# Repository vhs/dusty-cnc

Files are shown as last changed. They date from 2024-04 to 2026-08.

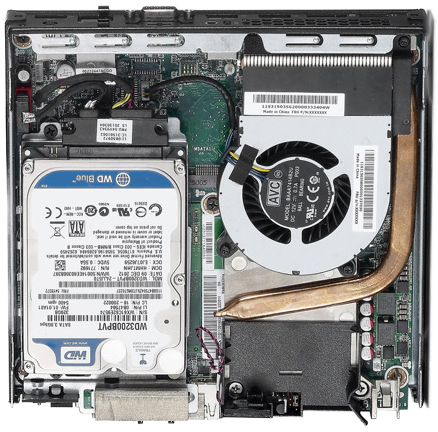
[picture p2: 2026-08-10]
documentation/wiring-diagram/components/Lenovo m73.png

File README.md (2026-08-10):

This repo contains files related to Dusty, the VHS wood CNC router.

- The repo is in a state of flux during the CNC rebuilding project
  - Files may move, disappear, or be created in large quantities
  - The machine name and repo name will change on release
  - It is always worth verifying with the project manager if you have up-to-date information
- Primary software used:
  - CAD software capable of reading/writing STEP files (such as FreeCAD, Rhino, Solidworks or Fusion360)
  - Draw.io (desktop or online) FOSS diagram software
  - Apple Numbers (an .xlsx export of the wiring chart exists for those who cannot access the main document, but should not be updated directly… this needs to be rectified)
- Notable files in the repo:
  - [Wiring Chart & BOM](https://github.com/vhs/dusty-cnc/blob/main/documentation/wiring-diagram/Dustie%20Wiring%20Chart.numbers) ([or read-only excel format](https://github.com/vhs/dusty-cnc/blob/main/documentation/wiring-diagram/Dustie%20Wiring%20Chart.export.xlsx))
  - [Wiring Diagram](https://github.com/vhs/dusty-cnc/blob/main/documentation/wiring-diagram/Wiring%20Diagram.drawio)
  - [CAD Assembly](https://github.com/vhs/dusty-cnc/blob/main/cad/Dustie%20Assembly.step) (not up to date)
- Notes:
  - Any questions please reach out to Martin ([@imagesurgery](https://github.com/imagesurgery))

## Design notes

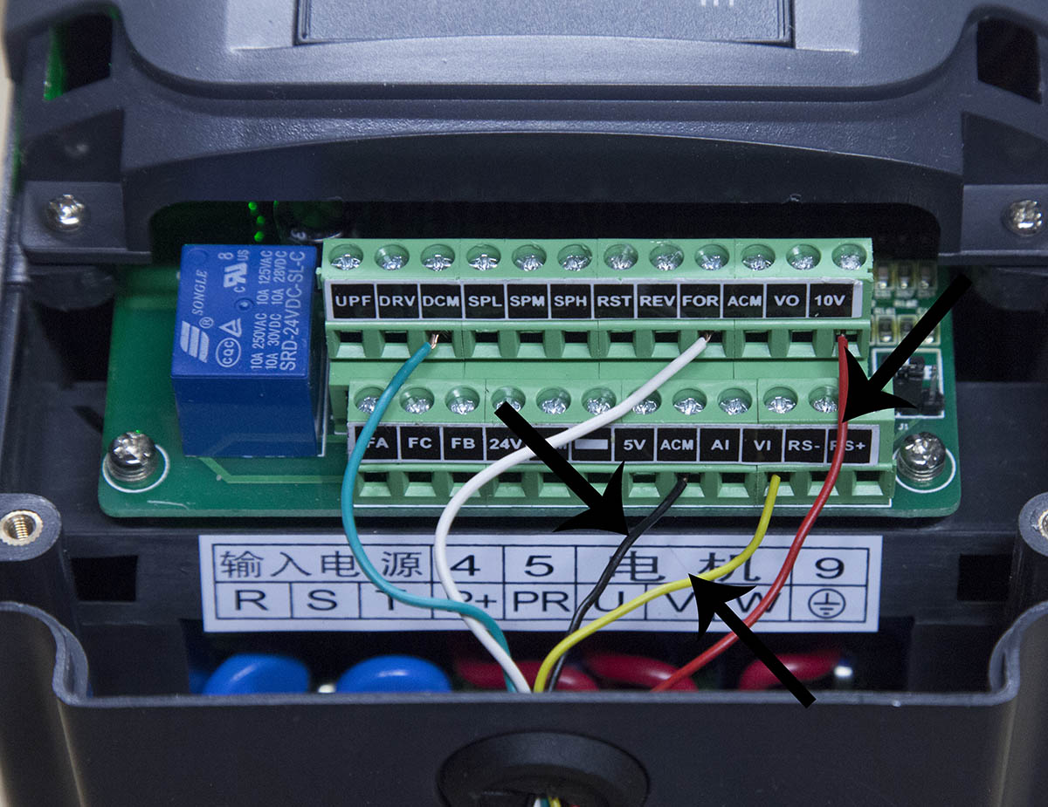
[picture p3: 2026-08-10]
documentation/manuals-datasheets/spindle/HY02D223B-pinout.jpeg

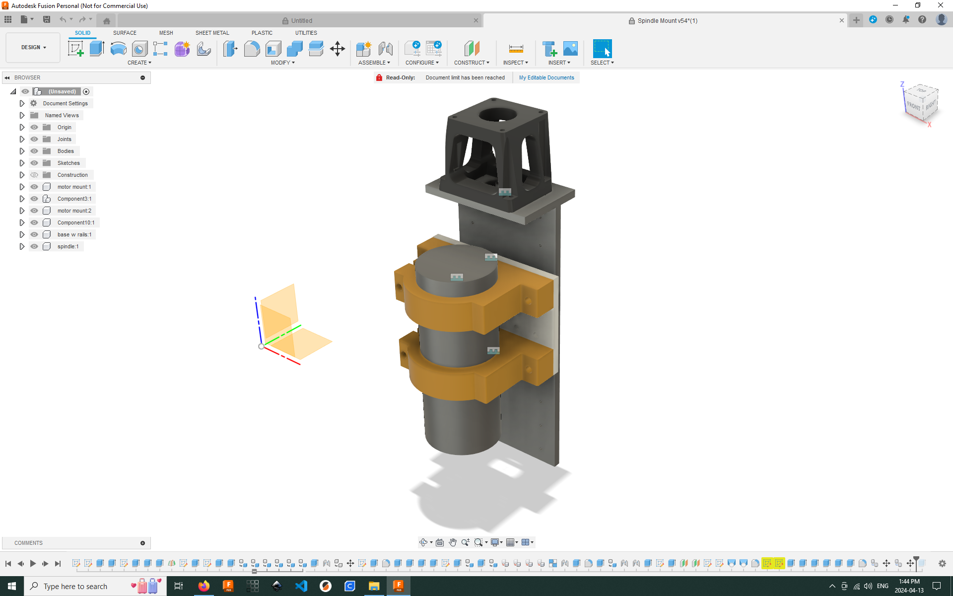
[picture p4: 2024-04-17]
Spindle Mount/spindle_mount_v54_preview.png

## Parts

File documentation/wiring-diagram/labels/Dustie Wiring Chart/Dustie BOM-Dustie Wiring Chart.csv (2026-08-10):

Tag | Type | Part / Model | Description | Mfr | Rating | Location | Mounting | Terminals | Used In | Qty | Spare | Notes
CPU1 | CPU |  | Tiny Form Factor Computer | Lenovo |  | CPU Cabinet | DIN Rail w. Printed Mount
F1 | EMI Filter |  |  |  |  | Main Cabinet | DIN Rail w. Printed Mount | 1-4
FAN1 | Fan |  |  |  | 24 VDC | Filter Box
FAN2 | Fan |  |  |  | 24 VDC | Filter Box
FAN3 | Fan |  |  |  |  | Filter Box
FAN4 | Fan |  |  |  |  | Filter Box
HS1 | Inductive Sensor |  | Y1 Home Switch |  |  | Static Platform | 8040 w. Printed Mount
HS2 | Inductive Sensor |  | Y2 Home Switch |  |  | Static Platform | 8040 w. Printed Mount
HS3 | Inductive Sensor |  | X Home Switch |  |  | Y Platform | 8040 w. Printed Mount
HS4 | Inductive Sensor |  | Z Home Switch |  |  | X Platform | Printed Mount
IM1 | Integrated Stepper | JSS57P2N | Y1 Integrated Stepper | Generic |  | Y Platform |  | Dir,Pul,Ena,Pend,Alm:[+/-] 5V,Tx,Gnd_SIG,Rx,NC; GND_PWR,+VDC
IM2 | Integrated Stepper | JSS57P2N | Y2 Integrated Stepper | Generic |  | Y Platform
IM3 | Integrated Stepper | JSS57P2N | X Integrated Stepper | Generic |  | X Platform
J1 | Connector | DB25-F to TB | Stepper and Sensor Signals |  |  | Main Cabinet Breakout | Panel Mount | 1-25,GND
J10 | Connector | PTB-2 | Sensor Power |  |  | Static Platform | Panel Mount | 1-2
J11 | Connector | PTB-8 | Integrated Stepper Power, Z Stepper Motor |  |  | Static Platform | Panel Mount | 1-8
J12 | Connector | PTB-8 | Estop Loop |  |  | Static Platform | Panel Mount | 1-8
J13 | Connector | PTB-4 | Estop Loop |  |  | Static Platform | Panel Mount | 1-4
J14 | Connector | DB25-F to TB |  |  |  | Static Platform | Panel Mount | 1-25,GND
J15 | Connector | PTB-4 | Sensor Power, Y1, Y2 Integrated Stepper Power |  |  | Static Platform | Panel Mount | 1-4
J16 | Connector | PTB-8 | X Integrated Stepper Power, Z Stepper Motor |  |  | Static Platform | Panel Mount | 1-8
J17 | Connector | PTB-4 | Estop Loop |  |  | MPG | Panel Mount | 1-4
J19 | Connector | DB25-F to TB |  |  |  | Y Platform | Panel Mount | 1-25,GND
J2 | Connector | PTB-2 | Sensor Power |  |  | Main Cabinet Breakout | Panel Mount | 1-2
J20 | Connector | PTB-4 | Sensor Power, Y1, Y2 Integrated Stepper Power |  |  | Y Platform | Panel Mount | 1-4
J24 | Connector | DB9-F to TB |  |  |  | Y Platform | Panel Mount | 1-9
J25 | Connector | PTB-2 | Sensor Power |  |  | Y Platform | Panel Mount | 1-2
J28 | Connector | DB9-F to TB |  |  |  | X Platform | Panel Mount | 1-9
J29 | Connector | PTB-2 | Sensor Power |  |  | X Platform | Panel Mount | 1-2
J3 | Connector | PTB-8 | Integrated Stepper Power, Z Stepper Motor |  |  | Main Cabinet Breakout | Panel Mount | 1-8
J30 | Connector | PTB-8 | X Integrated Stepper Power, Z Stepper Motor |  |  | X Platform | Panel Mount | 1-8
J35 | Connector |  | IEC C13 Socket |  |  | Main Cabinet Breakout | Panel Mount
J36 | Connector |  | IEC C7 Plug |  |  | Static Platform
J37 | Connector |  | HDMI Socket |  |  | Main Cabinet Breakout | Panel Mount | HDMI
J38 | Connector |  | USB Socket |  |  | Main Cabinet Breakout | Panel Mount | USB
J39 | Connector |  | USB Socket |  |  | CPU Cabinet | Panel Mount | USB
J4 | Connector | PTB-2 | Coolant Pump Relay |  |  | Main Cabinet Breakout | Panel Mount | 1-2
J5 | Connector | PTB-2 | Spindle Control |  |  | Main Cabinet Breakout | Panel Mount | 1-2
J6 | Connector | PTB-4 | X Integrated Stepper Power |  |  | Main Cabinet Breakout | Panel Mount | 1-4
J7 | Connector | PTB-8 | Estop Loop |  |  | Main Cabinet Breakout | Panel Mount | 1-8
J9 | Connector | DB25-F to TB |  |  |  | Static Platform | Panel Mount | 1-25,GND
K1 | Contactor |  |  |  |  | Main Cabinet | DIN Rail | L1-3,T1-3,13-14,21-22,A1,A2
K2 | Relay |  | Coolant Pump Relay |  |  |  |  |  |  |  |  | Need relay suitable for AC120V
LS1 | Inductive Sensor |  | Y- Limit Switch |  |  | Static Platform | 8040 w. Printed Mount
LS2 | Inductive Sensor |  | Y+ Limit Switch |  |  | Static Platform | 8040 w. Printed Mount
LS3 | Inductive Sensor |  | X- Limit Switch |  |  | Y Platform | 8040 w. Printed Mount
LS4 | Inductive Sensor |  | X+ Limit Switch |  |  | Y Platform | 8040 w. Printed Mount
LS5 | Inductive Sensor |  | Z- Limit Switch |  |  | X Platform | Printed Mount
LS6 | Inductive Sensor |  | Z+ Limit Switch |  |  | X Platform | Printed Mount
M1 | Spindle |  |  |  |  | Z Platform |  | 1(U),2(V),3(W),GND
MESA | FPGA Controller Card | 7i76EU |  | Mesa |  | Main Cabinet | DIN Rail w. Printed Mount | TB1,4:01-08;TB2-3,5-6:01-24
MON1 | Monitor |  | Touch Screen Monitor | Premio |  | Static Platform
P0 | Connector | HBL5666C | Nema 6-15P Plug | Hubbell |  | Power Entry |  | L1,L2,PE
P1 | Connector | DB25-M to TB |  |  |  | Main Cabinet Breakout | Panel Mount | 1-25,GND
P10 | Connector | PTB-2 | Sensor Power |  |  | Static Platform | Panel Mount | 1-2
P11 | Connector | PTB-8 | Integrated Stepper Power, Z Stepper Motor |  |  | Static Platform | Panel Mount | 1-8
P12 | Connector | PTB-8 | Estop Loop |  |  | Static Platform | Panel Mount | 1-8
P13 | Connector | PTB-4 | Estop Loop |  |  | Static Platform | Panel Mount | 1-4
P14 | Connector | DB25-M to TB |  |  |  | Static Platform | Panel Mount | 1-25,GND
P15 | Connector | PTB-4 | Sensor Power, Y1, Y2 Integrated Stepper Power |  |  | Static Platform | Panel Mount | 1-4
P16 | Connector | PTB-8 | X Integrated Stepper Power, Z Stepper Motor |  |  | Static Platform | Panel Mount | 1-8
P17 | Connector | PTB-4 | Estop Loop |  |  | MPG | Panel Mount | 1-4
P19 | Connector | DB25-M to TB |  |  |  | Y Platform | Panel Mount | 1-25,GND
P2 | Connector | PTB-2 | Sensor Power |  |  | Main Cabinet Breakout | Panel Mount | 1-2
P20 | Connector | PTB-4 | Sensor Power |  |  | Y Platform | Panel Mount | 1-4
P24 | Connector | DB9-M to TB |  |  |  | Y Platform | Panel Mount | 1-9
P25 | Connector | PTB-2 | Sensor Power |  |  | Y Platform | Panel Mount | 1-2
P28 | Connector | DB9-M to TB |  |  |  | X Platform | Panel Mount | 1-9
P29 | Connector | PTB-2 | Sensor Power |  |  | X Platform | Panel Mount | 1-2
P3 | Connector | PTB-8 | Y1, Y2 Integrated Stepper Power |  |  | Main Cabinet Breakout | Panel Mount | 1-8
P30 | Connector | PTB-8 | X Integrated Stepper Power |  |  | X Platform | Panel Mount | 1-8
P35 | Connector |  | IEC C14 Plug |  |  | Main Cabinet Breakout
P4 | Connector | PTB-2 | Coolant Pump Relay |  |  | Main Cabinet Breakout | Panel Mount | 1-2
P40 | Connector |  | IEC C5 Plug |  |  | CPU Cabinet |  | L,N,PE
P5 | Connector | PTB-2 | Spindle Control |  |  | Main Cabinet Breakout | Panel Mount | 1-2
P6 | Connector | PTB-4 | Spindle Power |  |  | Main Cabinet Breakout | Panel Mount | 1-4
P7 | Connector | PTB-8 | Estop Loop |  |  | Main Cabinet Breakout | Panel Mount | 1-8
P9 | Connector | DB25-M to TB |  |  |  | Static Platform | Panel Mount | 1-25,GND
PB1 | Momentary Button |  | Machine Start |  |  | Main Cabinet Door | Panel Mount | 13-14
PB2 | Momentary Button |  | Machine Stop |  |  | Main Cabinet Door | Panel Mount | 13-14
PL1 | Indicator Lamp |  | Main Estop Lamp |  |  | Main Cabinet Door | Panel Mount | X1-2
PL2 | Indicator Lamp |  | Machine Estop Lamp |  |  | Static Platform | Panel Mount | X1-2
PL3 | Indicator Lamp |  | MPG Estop Lamp |  |  | MPG | Panel Mount | X1-2
PL4 | Indicator Lamp |  | Machine Power Lamp |  |  | Main Cabinet Door | Panel Mount | X1-2
PS1 | PSU | HDR-15-24 | 24V 0.63A PSU | Mean Well | 24 VDC | Main Cabinet | DIN Rail
PS2 | PSU |  |  | Lenovo |  | CPU Cabinet | DIN Rail w. Printed Mount | L,N,PE
PS3 | PSU |  |  | Premio |  | Monitor Mount
PS4 | PSU |  |  | Mean Well | 24 VDC | Main Cabinet |  | L,N,GND,V+1,V+2,V-1,V-2
PS5 | PSU | S-350-48 | 48V 7.3A PSU | Generic | 48 VDC | Main Cabinet |  | L,N,GND,V+1,V+2,V+3,V-1,V-2,V-3
PS6 | PSU | S-350-48 | 48V 7.3A PSU | Generic | 48 VDC | Main Cabinet |  | L,N,GND,V+1,V+2,V+3,V-1,V-2,V-3
Q1 | MCB |  |  |  |  | Main Cabinet | DIN Rail | L1,L2,T1,T2
RF1 | Connector | ADP-SMAF-SMAF-F-G | WiFi Breakout |  |  | CPU Cabinet | Panel Mount | 1-2
RF2 | Antenna | SMA Antenna | WiFi Breakout |  |  | CPU Cabinet | SMA Screw Terminal | 1
S1 | Latching Estop |  | Main Estop |  |  | Main Cabinet Door | Panel Mount | 13-14,21-22
S2 | Latching Estop |  | Machine Estop |  |  | Static Platform | Box | 13-14,21-22
S3 | Latching Estop |  | MPG Estop |  |  | MPG | Panel Mount | 13-14,21-22
SD1 | Stepper Driver | HY-DIV268N-5A | Stepper Driver Z |  |  | Main Cabinet | DIN Rail w. Printed Mount | Dir,Pul,Ena,A,B,DC:[+/-]
SM1 | Stepper Motor | 57J1876-447-01 | Z Stepper Motor | Generic |  | X Platform
TB1 | Terminal Block | UK5N | 2-row DIN terminal | Phoenix Contact |  | Main Cabinet | DIN Rail | 1-6
TB10 | Terminal Block | UK5N | 2-row DIN terminal | Phoenix Contact |  | Main Cabinet | DIN Rail | 1-2
TB11 | Terminal Block | UK5N | 2-row DIN terminal | Phoenix Contact |  | Main Cabinet | DIN Rail | 1-26
TB2 | Terminal Block | UK5N | 2-row DIN terminal | Phoenix Contact |  | Main Cabinet | DIN Rail | 1-20
TB3 | Terminal Block | UK5N | 2-row DIN terminal | Phoenix Contact |  | Main Cabinet | DIN Rail | 1-20
TB4 | Terminal Block | UK5N | 2-row DIN terminal | Phoenix Contact |  | Main Cabinet | DIN Rail | 1-20
TB5 | Terminal Block | UK5N | 2-row DIN terminal | Phoenix Contact |  | Main Cabinet | DIN Rail | 1-18
TB51 | Terminal Block | PTFIX | 12P Push-in Distribution Block | Phoenix Contact |  | Static Platform |  | 1-12
TB52 | Terminal Block | PTFIX | 12P Push-in Distribution Block | Phoenix Contact |  | Static Platform |  | 1-12
TB53 | Terminal Block | PTFIX | 6P Push-in Distribution Block | Phoenix Contact |  | Y Platform |  | 1-6
TB54 | Terminal Block | PTFIX | 6P Push-in Distribution Block | Phoenix Contact |  | Y Platform |  | 1-6
TB55 | Terminal Block | PTFIX | 6P Push-in Distribution Block | Phoenix Contact |  | Y Platform |  | 1-6
TB56 | Terminal Block | PTFIX | 6P Push-in Distribution Block | Phoenix Contact |  | Y Platform |  | 1-6
TB57 | Terminal Block | PTFIX | 6P Push-in Distribution Block | Phoenix Contact |  | X Platform |  | 1-6
TB58 | Terminal Block | PTFIX | 6P Push-in Distribution Block | Phoenix Contact |  | X Platform |  | 1-6
TB6 | Terminal Block | UK5N | 2-row DIN terminal | Phoenix Contact |  | Main Cabinet | DIN Rail | 1-4
TB7 | Terminal Block | UK5N | 2-row DIN terminal | Phoenix Contact |  | Main Cabinet | DIN Rail | 1-6
TB8 | Terminal Block | UK5N | 2-row DIN terminal | Phoenix Contact |  | Main Cabinet | DIN Rail | 1-2
TB9 | Terminal Block | UK5N | 2-row DIN terminal | Phoenix Contact |  | Main Cabinet | DIN Rail | 1-2
TP1 | Passive Probe |  | Tool Touch Plate |  |  | Static Platform
TI1 | Temperature Indicator |  | Cabinet Temperature Sensor Module |  |  | Main Cabinet
VFD1 | VFD | HY02D223B |  | Huanyang | 220 VAC | VFD Cabinet | Metal Plate on VFD Cabinet | R,S,T,P+,PR,U,V,W,GND UPF,DRV,DCM,SPL,SPM,SPH,RST,REV,FOR,ACM,V0,10V FA,FC,FB,24V,COM,—,5V,ACM,AI,VI,RS-,RS+

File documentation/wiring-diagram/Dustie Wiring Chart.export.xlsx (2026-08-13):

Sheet: Export Summary
This document was exported from Numbers. Each table was converted to an Excel worksheet. All other objects on each Numbers sheet were placed on separate worksheets. Please be aware that formula calculations may differ in Excel.
Numbers Sheet Name | Numbers Table Name | Excel Worksheet Name
Dustie BOM
 | Dustie Wiring Chart | Dustie BOM - Dustie Wiring Char
Dustie Wires
 | Dustie Wiring Chart | Dustie Wires - Dustie Wiring Ch
Dustie Wire Labels
 | Dustie Wire Labels | Dustie Wire Labels - Dustie Wir

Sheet: Dustie BOM - Dustie Wiring Char
Dustie Wiring Chart
Tag | Type | Part / Model | Description | Location | Mounting | Terminals | Used In | Qty | Spare | Notes
CPU1 | CPU |  | Tiny Form Factor Computer | CPU Cabinet | DIN Rail w. Printed Mount
F1 | EMI Filter |  |  | Main Cabinet | DIN Rail w. Printed Mount | 1-4
FAN1 | Fan |  |  | Filter Box
FAN2 | Fan |  |  | Filter Box
FAN3 | Fan |  |  | Filter Box
FAN4 | Fan |  |  | Filter Box
HS1 | Inductive Sensor |  | Y1 Home Switch | Static Platform | 8040 w. Printed Mount
HS2 | Inductive Sensor |  | Y2 Home Switch | Static Platform | 8040 w. Printed Mount
HS3 | Inductive Sensor |  | X Home Switch | Y Platform | 8040 w. Printed Mount
HS4 | Inductive Sensor |  | Z Home Switch | X Platform | Printed Mount
IM1 | Integrated Stepper | JSS57P2N | Y1 Integrated Stepper | Y Platform |  | DIR,PUL,ENA,PEND,ALM:[+/-] 5V,TX,GND_SIG,RX,NC; GND_PWR,+VDC
IM2 | Integrated Stepper | JSS57P2N | Y2 Integrated Stepper | Y Platform
IM3 | Integrated Stepper | JSS57P2N | X Integrated Stepper | X Platform
J1 | Connector | DB25-F to TB | Stepper and Sensor Signals | Main Cabinet Breakout | Panel Mount | 1-25,GND
J10 | Connector | PTB-2 | Sensor Power | Static Platform | Panel Mount | 1-2
J11 | Connector | PTB-8 | Z, Dust Boot Stepper Motor | Static Platform | Panel Mount | 1-8
J12 | Connector | PTB-8 | Estop Loop | Static Platform | Panel Mount | 1-8
J13 | Connector | PTB-4 | Estop Loop | Static Platform | Panel Mount | 1-4
J14 | Connector | DB25-F to TB |  | Static Platform | Panel Mount | 1-25,GND
J15 | Connector | PTB-4 | Sensor Power, Y1, Y2 Integrated Stepper Power | Static Platform | Panel Mount | 1-4
J16 | Connector | PTB-8 | X Integrated Stepper Power, Z Stepper Motor | Static Platform | Panel Mount | 1-8
J17 | Connector | PTB-4 | Estop Loop | MPG | Panel Mount | 1-4
J18 | Connector | PTB-4 | Integrated Stepper Power | Static Platform | Panel Mount | 1-4
J19 | Connector | DB25-F to TB |  | Y Platform | Panel Mount | 1-25,GND
J2 | Connector | PTB-2 | Sensor Power | Main Cabinet Breakout | Panel Mount | 1-2
J20 | Connector | PTB-4 | Sensor Power, Y1, Y2 Integrated Stepper Power | Y Platform | Panel Mount | 1-4
J21 | Connector | PTB-2 | Sensor Power | Static Platform | Panel Mount | 1-2
J24 | Connector | DB9-F to TB |  | Y Platform | Panel Mount | 1-9
J25 | Connector | PTB-2 | Sensor Power | Y Platform | Panel Mount | 1-2
J28 | Connector | DB9-F to TB |  | X Platform | Panel Mount | 1-9
J29 | Connector | PTB-4 | Sensor Power | X Platform | Panel Mount | 1-4
J3 | Connector | PTB-8 | Z, Dust Boot Stepper Motor | Main Cabinet Breakout | Panel Mount | 1-8
J30 | Connector | PTB-8 | X Integrated Stepper Power, Z Stepper Motor | X Platform | Panel Mount | 1-8
J35 | Connector |  | IEC C13 Socket | Main Cabinet Breakout | Panel Mount
J36 | Connector |  | IEC C7 Plug | Static Platform
J37 | Connector |  | HDMI Socket | Main Cabinet Breakout | Panel Mount | HDMI
J38 | Connector |  | USB Socket | Main Cabinet Breakout | Panel Mount | USB
J39 | Connector |  | USB Socket | CPU Cabinet | Panel Mount | USB
J4 | Connector | PTB-2 | Coolant Pump Relay | Main Cabinet Breakout | Panel Mount | 1-2
J5 | Connector | PTB-2 | Spindle Control | Main Cabinet Breakout | Panel Mount | 1-2
J6 | Connector | PTB-4 | X Integrated Stepper Power | Main Cabinet Breakout | Panel Mount | 1-4
J7 | Connector | PTB-8 | Estop Loop | Main Cabinet Breakout | Panel Mount | 1-8
J8 | Connector | PTB-4 | Integrated Stepper Power | Main Cabinet Breakout | Panel Mount | 1-4
J9 | Connector | DB25-F to TB |  | Static Platform | Panel Mount | 1-25,GND
K1 | Contactor |  |  | Main Cabinet | DIN Rail | L1-3,T1-3,13-14,21-22,A1,A2
K2 | Relay |  | Coolant Pump Relay |  |  |  |  |  |  | Need relay suitable for AC120V
LS1 | Inductive Sensor |  | Y- Limit Switch | Static Platform | 8040 w. Printed Mount
LS2 | Inductive Sensor |  | Y+ Limit Switch | Static Platform | 8040 w. Printed Mount
LS3 | Inductive Sensor |  | X- Limit Switch | Y Platform | 8040 w. Printed Mount
LS4 | Inductive Sensor |  | X+ Limit Switch | Y Platform | 8040 w. Printed Mount
LS5 | Inductive Sensor |  | Z- Limit Switch | X Platform | Printed Mount
LS6 | Inductive Sensor |  | Z+ Limit Switch | X Platform | Printed Mount
M1 | Spindle |  |  | Z Platform |  | 1(U),2(V),3(W),GND
MESA | FPGA Controller Card | 7i76EU |  | Main Cabinet | DIN Rail w. Printed Mount | TB1,4:01-08;TB2-3,5-6:01-24
MON1 | Monitor |  | Touch Screen Monitor | Static Platform
P0 | Connector | HBL5666C | Nema 6-15P Plug | Power Entry |  | L1,L2,PE
P1 | Connector | DB25-M to TB |  | Main Cabinet Breakout | Panel Mount | 1-25,GND
P10 | Connector | PTB-2 | Sensor Power | Static Platform | Panel Mount | 1-2
P11 | Connector | PTB-8 | Z, Dust Boot Stepper Motor | Static Platform | Panel Mount | 1-8
P12 | Connector | PTB-8 | Estop Loop | Static Platform | Panel Mount | 1-8
P13 | Connector | PTB-4 | Estop Loop | Static Platform | Panel Mount | 1-4
P14 | Connector | DB25-M to TB |  | Static Platform | Panel Mount | 1-25,GND
P15 | Connector | PTB-4 | Sensor Power, Y1, Y2 Integrated Stepper Power | Static Platform | Panel Mount | 1-4
P16 | Connector | PTB-8 | X Integrated Stepper Power, Z Stepper Motor | Static Platform | Panel Mount | 1-8
P17 | Connector | PTB-4 | Estop Loop | MPG | Panel Mount | 1-4
P18 | Connector | PTB-4 | Integrated Stepper Power | Static Platform | Panel Mount | 1-4
P19 | Connector | DB25-M to TB |  | Y Platform | Panel Mount | 1-25,GND
P2 | Connector | PTB-2 | Sensor Power | Main Cabinet Breakout | Panel Mount | 1-2
P20 | Connector | PTB-4 | Sensor Power | Y Platform | Panel Mount | 1-4
P21 | Connector | PTB-2 | Sensor Power | Static Platform | Panel Mount | 1-2
P24 | Connector | DB9-M to TB |  | Y Platform | Panel Mount | 1-9
P25 | Connector | PTB-2 | Sensor Power | Y Platform | Panel Mount | 1-2
P28 | Connector | DB9-M to TB |  | X Platform | Panel Mount | 1-9
P29 | Connector | PTB-4 | Sensor Power | X Platform | Panel Mount | 1-4
P3 | Connector | PTB-8 | Z, Dust Boot Stepper Motor | Main Cabinet Breakout | Panel Mount | 1-8
P30 | Connector | PTB-8 | X Integrated Stepper Power | X Platform | Panel Mount | 1-8
P35 | Connector |  | IEC C14 Plug | Main Cabinet Breakout
P4 | Connector | PTB-2 | Coolant Pump Relay | Main Cabinet Breakout | Panel Mount | 1-2
P40 | Connector |  | IEC C5 Plug | CPU Cabinet |  | L,N,PE
P5 | Connector | PTB-2 | Spindle Control | Main Cabinet Breakout | Panel Mount | 1-2
P6 | Connector | PTB-4 | Spindle Power | Main Cabinet Breakout | Panel Mount | 1-4
P7 | Connector | PTB-8 | Estop Loop | Main Cabinet Breakout | Panel Mount | 1-8
P8 | Connector | PTB-4 | Y1, Y2 Integrated Stepper Power | Main Cabinet Breakout | Panel Mount | 1-4
P9 | Connector | DB25-M to TB |  | Static Platform | Panel Mount | 1-25,GND
PB1 | Momentary Button |  | Machine Start | Main Cabinet Door | Panel Mount | 13-14
PB2 | Momentary Button |  | Machine Stop | Main Cabinet Door | Panel Mount | 13-14
PL1 | Indicator Lamp |  | Main Estop Lamp | Main Cabinet Door | Panel Mount | X1-2
PL2 | Indicator Lamp |  | Machine Estop Lamp | Static Platform | Panel Mount | X1-2
PL3 | Indicator Lamp |  | MPG Estop Lamp | MPG | Panel Mount | X1-2
PL4 | Indicator Lamp |  | Machine Power Lamp | Main Cabinet Door | Panel Mount | X1-2
PS1 | PSU | HDR-15-24 | 24V 0.63A PSU | Main Cabinet | DIN Rail
PS2 | PSU |  |  | CPU Cabinet | DIN Rail w. Printed Mount | L,N,PE
PS3 | PSU |  |  | Monitor Mount
PS4 | PSU |  |  | Main Cabinet |  | L,N,GND,V+1,V+2,V-1,V-2
PS5 | PSU | S-350-48 | 48V 7.3A PSU | Main Cabinet |  | L,N,GND,V+1,V+2,V+3,V-1,V-2,V-3
PS6 | PSU | S-350-48 | 48V 7.3A PSU | Main Cabinet |  | L,N,GND,V+1,V+2,V+3,V-1,V-2,V-3
Q1 | MCB |  |  | Main Cabinet | DIN Rail | L1,L2,T1,T2
RF1 | Connector | ADP-SMAF-SMAF-F-G | WiFi Breakout | CPU Cabinet | Panel Mount | 1-2
RF2 | Antenna | SMA Antenna | WiFi Breakout | CPU Cabinet | SMA Screw Terminal | 1
S1 | Latching Estop |  | Main Estop | Main Cabinet Door | Panel Mount | 13-14,21-22
S2 | Latching Estop |  | Machine Estop | Static Platform | Box | 13-14,21-22
S3 | Latching Estop |  | MPG Estop | MPG | Panel Mount | 13-14,21-22
SD1 | Stepper Driver | HY-DIV268N-5A | Stepper Driver Z | Main Cabinet | DIN Rail w. Printed Mount | DIR,PUL,ENA,A,B,DC:[+/-]
SD2 | Stepper Driver | HY-DIV268N-5A-ish | Stepper Driver Dust Boot | Main Cabinet | DIN Rail w. Printed Mount | DIR,PUL,ENA,A,B,DC:[+/-]
SM1 | Stepper Motor | 57J1876-447-01 | Z Stepper Motor | X Platform
TB1 | Terminal Block | UK5N | 2-row DIN terminal | Main Cabinet | DIN Rail | 1-6
TB10 | Terminal Block | UK5N | 2-row DIN terminal | Main Cabinet | DIN Rail | 1-2
TB11 | Terminal Block | UK5N | 2-row DIN terminal | Main Cabinet | DIN Rail | 1-26
TB2 | Terminal Block | UK5N | 2-row DIN terminal | Main Cabinet | DIN Rail | 1-20
TB3 | Terminal Block | UK5N | 2-row DIN terminal | Main Cabinet | DIN Rail | 1-20
TB4 | Terminal Block | UK5N | 2-row DIN terminal | Main Cabinet | DIN Rail | 1-20
TB5 | Terminal Block | UK5N | 2-row DIN terminal | Main Cabinet | DIN Rail | 1-18
TB51 | Terminal Block | PTFIX | 12P Push-in Distribution Block | Static Platform |  | 1-12
TB52 | Terminal Block | PTFIX | 12P Push-in Distribution Block | Static Platform |  | 1-12
TB53 | Terminal Block | PTFIX | 6P Push-in Distribution Block | Y Platform |  | 1-6
TB54 | Terminal Block | PTFIX | 6P Push-in Distribution Block | Y Platform |  | 1-6
TB55 | Terminal Block | PTFIX | 6P Push-in Distribution Block | Y Platform |  | 1-6
TB56 | Terminal Block | PTFIX | 6P Push-in Distribution Block | Y Platform |  | 1-6
TB57 | Terminal Block | PTFIX | 6P Push-in Distribution Block | X Platform |  | 1-6
TB58 | Terminal Block | PTFIX | 6P Push-in Distribution Block | X Platform |  | 1-6
TB6 | Terminal Block | UK5N | 2-row DIN terminal | Main Cabinet | DIN Rail | 1-4
TB7 | Terminal Block | UK5N | 2-row DIN terminal | Main Cabinet | DIN Rail | 1-6
TB8 | Terminal Block | UK5N | 2-row DIN terminal | Main Cabinet | DIN Rail | 1-2
TB9 | Terminal Block | UK5N | 2-row DIN terminal | Main Cabinet | DIN Rail | 1-2
TI1 | Temperature Indicator |  | Cabinet Temperature Sensor Module | Main Cabinet
TP1 | Passive Probe |  | Tool Touch Plate | Static Platform
VFD1 | VFD | HY02D223B |  | VFD Cabinet | Metal Plate on VFD Cabinet | R,S,T,P+,PR,U,V,W,GND UPF,DRV,DCM,SPL,SPM,SPH,RST,REV,FOR,ACM,V0,10V FA,FC,FB,24V,COM,—,5V,ACM,AI,VI,RS-,RS+

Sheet: Dustie Wires - Dustie Wiring Ch
Dustie Wiring Chart
Wire | Wire From | Wire To | Zone | Location | Signal | From Device | From Mesa TB | From Terminal | From Type | To Device | To Mesa TB | To Terminal | To Type | AWG | Flex | Length | Colour | Notes
W·001 | → TB1:5 | P0:L1→ | 240V Power | Main Cabinet | AC_L1_IN | P0 |  | L1 | OTHER | TB1 |  | 5 | FERRULE | 10 | FALSE |  | 🟥 Red
W·002 | → TB1:3 | P0:L2→ | 240V Power | Main Cabinet | AC_L2_IN | P0 |  | L2 | OTHER | TB1 |  | 3 | FERRULE | 10 | FALSE |  | ⬛️ Black
W·003 | → Q1:1 | TB1:6→ | 240V Power | Main Cabinet | AC_L1_IN | TB1 |  | 6 | FERRULE | Q1 |  | 1 | FERRULE | 10 | FALSE |  | 🟥 Red
W·004 | → Q1:3 | TB1:4→ | 240V Power | Main Cabinet | AC_L2_IN | TB1 |  | 4 | FERRULE | Q1 |  | 3 | FERRULE | 10 | FALSE |  | ⬛️ Black
W·005 | → F1:1 | Q1:2→ | 240V Power | Main Cabinet | AC_L1_FUSED | Q1 |  | 2 | FERRULE | F1 |  | 1 | RING | 10 | FALSE |  | 🟥 Red
W·006 | → F1:2 | Q1:4→ | 240V Power | Main Cabinet | AC_L2_FUSED | Q1 |  | 4 | FERRULE | F1 |  | 2 | RING | 10 | FALSE |  | ⬛️ Black
W·007 | → TB2:1 | F1:3→ | 240V Power | Main Cabinet | AC_L1_FILTERED | F1 |  | 3 | RING | TB2 |  | 1 | FERRULE | 10 | FALSE |  | 🟥 Red
W·008 | → TB2:11 | F1:4→ | 240V Power | Main Cabinet | AC_L2_FILTERED | F1 |  | 4 | RING | TB2 |  | 11 | FERRULE | 10 | FALSE |  | ⬛️ Black
W·009 | → PS1:L | TB2:10→ | 240V Power | Main Cabinet | AC_L1_FILTERED | TB2 |  | 10 | FERRULE | PS1 |  | L | FERRULE | 14 | FALSE |  | 🟥 Red
W·010 | → PS1:N | TB2:20→ | 240V Power | Main Cabinet | AC_L2_FILTERED | TB2 |  | 20 | FERRULE | PS1 |  | N | FERRULE | 14 | FALSE |  | ⬛️ Black
W·011 | → K1:L1 | TB2:8→ | 240V Power | Main Cabinet | AC_L1_FILTERED | TB2 |  | 8 | FERRULE | K1 |  | L1 | RING | 10 | FALSE |  | 🟥 Red
W·012 | → K1:L2 | TB2:18→ | 240V Power | Main Cabinet | AC_L2_FILTERED | TB2 |  | 18 | FERRULE | K1 |  | L2 | RING | 10 | FALSE |  | ⬛️ Black
W·013 | → PS2:L | TB2:6→ | 240V Power | Main Cabinet | AC_L1_FILTERED | TB2 |  | 6 | FERRULE | PS2 |  | L | OTHER | 10 | FALSE |  | ⬛️ Black | Wire is black because of the preformed C5 connector end
W·014 | → PS2:N | TB2:16→ | 240V Power | Main Cabinet | AC_L2_FILTERED | TB2 |  | 16 | FERRULE | PS2 |  | N | OTHER | 10 | FALSE |  | ⬛️ Black
W·015 | → J35:L | TB2:4→ | 240V Power | Main Cabinet | AC_L1_FILTERED | TB2 |  | 4 | FERRULE | J35 |  | L | BLADE | 10 | FALSE |  | 🟥 Red
W·016 | → J35:N | TB2:14→ | 240V Power | Main Cabinet | AC_L2_FILTERED | TB2 |  | 14 | FERRULE | J35 |  | N | BLADE | 10 | FALSE |  | ⬛️ Black
W·021 | → TB3:1 | K1:T1→ | 240V Power | Main Cabinet | AC_L1_FILTERED | K1 |  | T1 | RING | TB3 |  | 1 | FERRULE | 10 | FALSE |  | 🟥 Red
W·022 | → TB3:11 | K1:T2→ | 240V Power | Main Cabinet | AC_L2_FILTERED | K1 |  | T2 | RING | TB3 |  | 11 | FERRULE | 10 | FALSE |  | ⬛️ Black
W·023 | → PS5:L | TB3:10→ | 240V Power | Main Cabinet | AC_L1_FILTERED | TB3 |  | 10 | FERRULE | PS5 |  | L | RING | 10 | FALSE |  | 🟥 Red
W·024 | → PS5:N | TB3:20→ | 240V Power | Main Cabinet | AC_L2_FILTERED | TB3 |  | 20 | FERRULE | PS5 |  | N | RING | 10 | FALSE |  | ⬛️ Black
W·025 | → PS6:L | TB3:8→ | 240V Power | Main Cabinet | AC_L1_FILTERED | TB3 |  | 8 | FERRULE | PS6 |  | L | RING | 10 | FALSE |  | 🟥 Red
W·026 | → PS6:N | TB3:18→ | 240V Power | Main Cabinet | AC_L2_FILTERED | TB3 |  | 18 | FERRULE | PS6 |  | N | RING | 10 | FALSE |  | ⬛️ Black
W·027 | → PS4:L | TB3:6→ | 240V Power | Main Cabinet | AC_L1_FILTERED | TB3 |  | 6 | FERRULE | PS4 |  | L | FERRULE | 10 | FALSE |  | 🟥 Red
W·028 | → PS4:N | TB3:16→ | 240V Power | Main Cabinet | AC_L2_FILTERED | TB3 |  | 16 | FERRULE | PS4 |  | N | FERRULE | 10 | FALSE |  | ⬛️ Black
W·029 | → J6:4 | TB3:4→ | 240V Power | Main Cabinet | AC_L1_FILTERED | TB3 |  | 4 | FERRULE | J6 |  | 4 | FERRULE | 10 | FALSE |  | 🟥 Red
W·030 | → J6:3 | TB3:14→ | 240V Power | Main Cabinet | AC_L2_FILTERED | TB3 |  | 14 | FERRULE | J6 |  | 3 | FERRULE | 10 | FALSE |  | ⬛️ Black
W·051 | → VFD1:R | P6:4→ | 240V Power | Field | AC_L1_FILTERED | P6 |  | 4 | FERRULE | VFD1 |  | R | FERRULE | 10 | FALSE |  | 🟥 Red
W·052 | → VFD1:S | P6:3→ | 240V Power | Field | AC_L2_FILTERED | P6 |  | 3 | FERRULE | VFD1 |  | S | FERRULE | 10 | FALSE |  | ⬛️ Black
W·053 | → J36:L | P35:L→ | 240V Power | Field | AC_L1_FILTERED | P35 |  | L | OTHER | J36 |  | L | OTHER | 14 | FALSE |  | 🟥 Red
W·054 | → J36:N | P35:N→ | 240V Power | Field | AC_L2_FILTERED | P35 |  | N | OTHER | J36 |  | N | OTHER | 14 | FALSE |  | ⬛️ Black
W·101 | → TB5:1 | PS1:V+→ | Estop/Power Mgmt | Main Cabinet | 24V_LOGIC | PS1 |  | V+ | FERRULE | TB5 |  | 1 | FERRULE | 18 | FALSE |  | 🟦 Blue
W·102 | → TB5:9 | PS1:V-→ | Estop/Power Mgmt | Main Cabinet | 0V_LOGIC | PS1 |  | V- | FERRULE | TB5 |  | 9 | FERRULE | 18 | FALSE |  | 🟦⬜️ Blue/White
W·103 | → S1:21 | TB5:8→ | Estop/Power Mgmt | Main Cabinet | 24V_LOGIC | TB5 |  | 8 | FERRULE | S1 |  | 21 | FERRULE | 18 | FALSE |  | 🟦 Blue | 21==NC
W·104 | → S1:13 | TB5:6→ | Estop/Power Mgmt | Main Cabinet | 24V_LOGIC | TB5 |  | 6 | FERRULE | S1 |  | 13 | FERRULE | 18 | FALSE |  | 🟦 Blue | 13==NO
W·105 | → J7:7 | TB5:4→ | Estop/Power Mgmt | Main Cabinet | 24V_LOGIC | TB5 |  | 4 | FERRULE | J7 |  | 7 | FERRULE | 18 | FALSE |  | 🟦 Blue
W·106 | → J7:3 | TB5:2→ | Estop/Power Mgmt | Main Cabinet | 24V_LOGIC | TB5 |  | 2 | FERRULE | J7 |  | 3 | FERRULE | 18 | FALSE |  | 🟦 Blue
W·107 | → PL1:X1 | TB5:18→ | Estop/Power Mgmt | Main Cabinet | ESTOP_INDICATOR | TB5 |  | 18 | FERRULE | PL1 |  | X1 | FERRULE | 18 | FALSE |  | 🟦⬜️ Blue/White
W·108 | → J7:6 | TB5:16→ | Estop/Power Mgmt | Main Cabinet | ESTOP_INDICATOR | TB5 |  | 16 | FERRULE | J7 |  | 6 | FERRULE | 18 | FALSE |  | 🟦⬜️ Blue/White
W·109 | → J7:2 | TB5:14→ | Estop/Power Mgmt | Main Cabinet | ESTOP_INDICATOR | TB5 |  | 14 | FERRULE | J7 |  | 2 | FERRULE | 18 | FALSE |  | 🟦⬜️ Blue/White
W·110 | → PL4:X2 | TB5:12→ | Estop/Power Mgmt | Main Cabinet | 0V_LOGIC | TB5 |  | 12 | FERRULE | PL4 |  | X2 | FERRULE | 18 | FALSE |  | 🟦⬜️ Blue/White
W·111 | → K1:A2 | TB5:10→ | Estop/Power Mgmt | Main Cabinet | 0V_LOGIC | TB5 |  | 10 | FERRULE | K1 |  | A2 | FERRULE | 18 | FALSE |  | 🟦⬜️ Blue/White
W·112 | → TB8:1 | S1:22→ | Estop/Power Mgmt | Main Cabinet | ESTOP_LOOP | S1 |  | 22 | FERRULE | TB8 |  | 1 | FERRULE | 18 | FALSE |  | 🟦 Blue | 22==NC
W·113 | → J7:8 | TB8:2→ | Estop/Power Mgmt | Main Cabinet | ESTOP_LOOP | TB8 |  | 2 | FERRULE | J7 |  | 8 | FERRULE | 18 | FALSE |  | 🟦 Blue
W·114 | → PL1:X2 | S1:14→ | Estop/Power Mgmt | Main Cabinet | 24V_LOGIC | S1 |  | 14 | FERRULE | PL1 |  | X2 | FERRULE | 18 | FALSE |  | 🟦 Blue | 14==NO
W·115 | → TB9:1 | J7:5→ | Estop/Power Mgmt | Main Cabinet | ESTOP_LOOP | J7 |  | 5 | FERRULE | TB9 |  | 1 | FERRULE | 18 | FALSE |  | 🟦 Blue
W·116 | → J7:4 | TB9:2→ | Estop/Power Mgmt | Main Cabinet | ESTOP_LOOP | TB9 |  | 2 | FERRULE | J7 |  | 4 | FERRULE | 18 | FALSE |  | 🟦 Blue
W·117 | → TB10:1 | J7:1→ | Estop/Power Mgmt | Main Cabinet | ESTOP_LOOP | J7 |  | 1 | FERRULE | TB10 |  | 1 | FERRULE | 18 | FALSE |  | 🟦 Blue
W·118 | → PB2:21 | TB10:2→ | Estop/Power Mgmt | Main Cabinet | ESTOP_LOOP | TB10 |  | 2 | FERRULE | PB2 |  | 21 | FERRULE | 18 | FALSE |  | 🟦 Blue | 21==NC
W·119 | → TB6:1 | PB2:22→ | Estop/Power Mgmt | Main Cabinet | ESTOP_LOOP | PB2 |  | 22 | FERRULE | TB6 |  | 1 | FERRULE | 18 | FALSE |  | 🟦 Blue | 22==NC
W·120 | → PB1:13 | TB6:2→ | Estop/Power Mgmt | Main Cabinet | ESTOP_LOOP | TB6 |  | 2 | FERRULE | PB1 |  | 13 | FERRULE | 18 | FALSE |  | 🟦 Blue | 13==NO
W·121 | → K1:13 | TB6:4→ | Estop/Power Mgmt | Main Cabinet | ESTOP_LOOP | TB6 |  | 4 | FERRULE | K1 |  | 13 | FERRULE | 18 | FALSE |  | 🟦 Blue | 13==NO
W·122 | → TB7:1 | PB1:14→ | Estop/Power Mgmt | Main Cabinet | MACHINE_ENABLE | PB1 |  | 14 | FERRULE | TB7 |  | 1 | FERRULE | 18 | FALSE |  | 🟦 Blue | 14==NO
W·123 | → K1:14 | TB7:4→ | Estop/Power Mgmt | Main Cabinet | MACHINE_ENABLE | TB7 |  | 4 | FERRULE | K1 |  | 14 | FERRULE | 18 | FALSE |  | 🟦 Blue | 14==NO
W·124 | → K1:A1 | TB7:6→ | Estop/Power Mgmt | Main Cabinet | MACHINE_ENABLE | TB7 |  | 6 | FERRULE | K1 |  | A1 | FERRULE | 18 | FALSE |  | 🟦 Blue
W·125 | → PL4:X1 | TB7:2→ | Estop/Power Mgmt | Main Cabinet | MACHINE_ENABLE | TB7 |  | 2 | FERRULE | PL4 |  | X1 | FERRULE | 18 | FALSE |  | 🟦 Blue
W·151 | → P12:8 | P7:8→ | Estop/Power Mgmt | Field | ESTOP_LOOP | P7 |  | 8 | FERRULE | P12 |  | 8 | FERRULE | 18 | FALSE |  | 🟦 Blue
W·152 | → P12:7 | P7:7→ | Estop/Power Mgmt | Field | 24V_LOGIC | P7 |  | 7 | FERRULE | P12 |  | 7 | FERRULE | 18 | FALSE |  | 🟦 Blue
W·153 | → P12:6 | P7:6→ | Estop/Power Mgmt | Field | ESTOP_INDICATOR | P7 |  | 6 | FERRULE | P12 |  | 6 | FERRULE | 18 | FALSE |  | 🟦⬜️ Blue/White
W·154 | → P12:5 | P7:5→ | Estop/Power Mgmt | Field | ESTOP_LOOP | P7 |  | 5 | FERRULE | P12 |  | 5 | FERRULE | 18 | FALSE |  | 🟦 Blue
W·155 | → S2:21 | J12:8→ | Estop/Power Mgmt | Field | ESTOP_LOOP | J12 |  | 8 | FERRULE | S2 |  | 21 | FERRULE | 18 | FALSE |  | 🟦 Blue | 21==NC
W·156 | → S2:13 | J12:7→ | Estop/Power Mgmt | Field | 24V_LOGIC | J12 |  | 7 | FERRULE | S2 |  | 13 | FERRULE | 18 | FALSE |  | 🟦 Blue | 13==NO
W·157 | → J12:6 | PL2:X2→ | Estop/Power Mgmt | Field | ESTOP_INDICATOR | PL2 |  | X2 | FERRULE | J12 |  | 6 | FERRULE | 18 | FALSE |  | 🟦⬜️ Blue/White
W·158 | → J12:5 | S2:22→ | Estop/Power Mgmt | Field | ESTOP_LOOP | S2 |  | 22 | FERRULE | J12 |  | 5 | FERRULE | 18 | FALSE |  | 🟦 Blue | 22==NC
W·159 | → PL2:X1 | S2:14→ | Estop/Power Mgmt | Field | 24V_LOGIC | S2 |  | 14 | FERRULE | PL2 |  | X1 | FERRULE | 18 | FALSE |  | 🟦 Blue | 14==NO
W·161 | → P12:4 | P7:4→ | Estop/Power Mgmt | Field | ESTOP_LOOP | P7 |  | 4 | FERRULE | P12 |  | 4 | FERRULE | 18 | FALSE |  | 🟦 Blue
W·162 | → P12:3 | P7:3→ | Estop/Power Mgmt | Field | 24V_LOGIC | P7 |  | 3 | FERRULE | P12 |  | 3 | FERRULE | 18 | FALSE |  | 🟦 Blue
W·163 | → P12:2 | P7:2→ | Estop/Power Mgmt | Field | ESTOP_INDICATOR | P7 |  | 2 | FERRULE | P12 |  | 2 | FERRULE | 18 | FALSE |  | 🟦⬜️ Blue/White
W·164 | → P12:1 | P7:1→ | Estop/Power Mgmt | Field | ESTOP_LOOP | P7 |  | 1 | FERRULE | P12 |  | 1 | FERRULE | 18 | FALSE |  | 🟦 Blue
W·165 | → J13:4 | P12:4→ | Estop/Power Mgmt | Field | ESTOP_LOOP | P12 |  | 4 | FERRULE | J13 |  | 4 | FERRULE | 18 | FALSE |  | 🟦 Blue
W·166 | → J13:3 | P12:3→ | Estop/Power Mgmt | Field | 24V_LOGIC | P12 |  | 3 | FERRULE | J13 |  | 3 | FERRULE | 18 | FALSE |  | 🟦 Blue
W·167 | → J13:2 | P12:2→ | Estop/Power Mgmt | Field | ESTOP_INDICATOR | P12 |  | 2 | FERRULE | J13 |  | 2 | FERRULE | 18 | FALSE |  | 🟦⬜️ Blue/White
W·168 | → J13:1 | P12:1→ | Estop/Power Mgmt | Field | ESTOP_LOOP | P12 |  | 1 | FERRULE | J13 |  | 1 | FERRULE | 18 | FALSE |  | 🟦 Blue
W·169 | → P17:4 | P13:4→ | Estop/Power Mgmt | Field | ESTOP_LOOP | P13 |  | 4 | FERRULE | P17 |  | 4 | FERRULE | 18 | TRUE |  | 🟦 Blue | Flex optional
W·170 | → P17:3 | P13:3→ | Estop/Power Mgmt | Field | 24V_LOGIC | P13 |  | 3 | FERRULE | P17 |  | 3 | FERRULE | 18 | TRUE |  | 🟦 Blue | Flex optional
W·171 | → P17:2 | P13:2→ | Estop/Power Mgmt | Field | ESTOP_INDICATOR | P13 |  | 2 | FERRULE | P17 |  | 2 | FERRULE | 18 | TRUE |  | 🟦⬜️ Blue/White | Flex optional
W·172 | → P17:1 | P13:1→ | Estop/Power Mgmt | Field | ESTOP_LOOP | P13 |  | 1 | FERRULE | P17 |  | 1 | FERRULE | 18 | TRUE |  | 🟦 Blue | Flex optional
W·173 | → S3:21 | J17:4→ | Estop/Power Mgmt | Field | ESTOP_LOOP | J17 |  | 4 | FERRULE | S3 |  | 21 | FERRULE | 18 | FALSE |  | 🟦 Blue | 21==NC
W·174 | → S3:13 | J17:3→ | Estop/Power Mgmt | Field | 24V_LOGIC | J17 |  | 3 | FERRULE | S3 |  | 13 | FERRULE | 18 | FALSE |  | 🟦 Blue | 13==NO
W·175 | → J17:2 | PL3:X2→ | Estop/Power Mgmt | Field | ESTOP_INDICATOR | PL3 |  | X2 | FERRULE | J17 |  | 2 | FERRULE | 18 | FALSE |  | 🟦⬜️ Blue/White
W·176 | → J17:1 | S3:22→ | Estop/Power Mgmt | Field | ESTOP_LOOP | S3 |  | 22 | FERRULE | J17 |  | 1 | FERRULE | 18 | FALSE |  | 🟦 Blue | 22==NC
W·177 | → PL3:X1 | S3:14→ | Estop/Power Mgmt | Field | 24V_LOGIC | S3 |  | 14 | FERRULE | PL3 |  | X1 | FERRULE | 18 | FALSE |  | 🟦 Blue | 14==NO
W·201 | → TB11:1 | PS4:V+1→ | 24V Power | Main Cabinet | 24V_LOGIC | PS4 |  | V+1 | FERRULE | TB11 |  | 1 | FERRULE | 18 | FALSE |  | 🟦 Blue
W·202 | → TB11:13 | PS4:V-1→ | 24V Power | Main Cabinet | 0V_LOGIC | PS4 |  | V-1 | FERRULE | TB11 |  | 13 | FERRULE | 18 | FALSE |  | 🟦⬜️ Blue/White
W·203 | → MESA:TB3:22 | TB11:2→ | 24V Power | Main Cabinet | 24V_LOGIC | TB11 |  | 2 | FERRULE | MESA | TB3 | 22 | FERRULE | 18 | FALSE |  | 🟦 Blue
W·204 | → MESA:TB3:24 | TB11:14→ | 24V Power | Main Cabinet | 0V_LOGIC | TB11 |  | 14 | FERRULE | MESA | TB3 | 24 | FERRULE | 18 | FALSE |  | 🟦⬜️ Blue/White
W·205 | → MESA:TB1:5 | TB11:4→ | 24V Power | Main Cabinet | 24V_LOGIC | TB11 |  | 4 | FERRULE | MESA | TB1 | 5 | FERRULE | 18 | FALSE |  | 🟦 Blue
W·206 | → MESA:TB1:8 | TB11:16→ | 24V Power | Main Cabinet | 0V_LOGIC | TB11 |  | 16 | FERRULE | MESA | TB1 | 8 | FERRULE | 18 | FALSE |  | 🟦⬜️ Blue/White
W·207 | → FANS1:1 | TB11:6→ | 24V Power | Main Cabinet | FAN_PWR | TB11 |  | 6 | FERRULE | FANS1 |  | 1 | FERRULE | 18 | FALSE |  | 🟦 Blue
W·208 | → FANS1:2 | TB11:18→ | 24V Power | Main Cabinet | 0V_LOGIC | TB11 |  | 18 | FERRULE | FANS1 |  | 2 | FERRULE | 18 | FALSE |  | 🟦⬜️ Blue/White
W·209 | → J2:1 | TB11:8→ | 24V Power | Main Cabinet | 24V_LOGIC | TB11 |  | 8 | FERRULE | J2 |  | 1 | FERRULE | 18 | FALSE |  | 🟦 Blue
W·210 | → J2:2 | TB11:20→ | 24V Power | Main Cabinet | 0V_LOGIC | TB11 |  | 20 | FERRULE | J2 |  | 2 | FERRULE | 18 | FALSE |  | 🟦⬜️ Blue/White
W·211 | → TI1:V+ | TB11:10→ | 24V Power | Main Cabinet | 24V_LOGIC | TB11 |  | 10 | FERRULE | TI1 |  | V+ | FERRULE | 18 | FALSE |  | 🟦 Blue
W·212 | → TI1:V- | TB11:22→ | 24V Power | Main Cabinet | 0V_LOGIC | TB11 |  | 22 | FERRULE | TI1 |  | V- | FERRULE | 18 | FALSE |  | 🟦⬜️ Blue/White
W·213 | → J4:2 | MESA:TB6:17→ | 24V Power | Main Cabinet | 24V_LOGIC | MESA | TB6 | 17 | FERRULE | J4 |  | 2 | FERRULE | 18 | FALSE |  | 🟦 Blue
W·214 | → J4:1 | TB11:24→ | 24V Power | Main Cabinet | 0V_LOGIC | TB11 |  | 24 | FERRULE | J4 |  | 1 | FERRULE | 18 | FALSE |  | 🟦⬜️ Blue/White
W·215 | → TI1:SIG | MESA:TB6:1→ | 24V Power | Main Cabinet | TI1_VSENSE | MESA | TB6 | 1 | FERRULE | TI1 |  | SIG | FERRULE | 18 | FALSE |  | 🟦 Blue
W·301 | → P10:2 | P2:2→ | 24V Power | Field | 24V_LOGIC | P2 |  | 2 | FERRULE | P10 |  | 2 | FERRULE | 18 | FALSE |  | 🟦 Blue
W·302 | → P10:1 | P2:1→ | 24V Power | Field | 0V_LOGIC | P2 |  | 1 | FERRULE | P10 |  | 1 | FERRULE | 18 | FALSE |  | 🟦⬜️ Blue/White
W·303 | → TB51:1 | J10:2→ | 24V Power | Field | 24V_LOGIC | J10 |  | 2 | FERRULE | TB51 |  | 1 | FERRULE | 18 | FALSE |  | 🟦 Blue
W·304 | → TB52:1 | J10:1→ | 24V Power | Field | 0V_LOGIC | J10 |  | 1 | FERRULE | TB52 |  | 1 | FERRULE | 18 | FALSE |  | 🟦⬜️ Blue/White
W·305 | → J21:1 | TB51:2→ | 24V Power | Field | 24V_LOGIC | TB51 |  | 2 | FERRULE | J21 |  | 1 | FERRULE | 18 | FALSE |  | 🟦 Blue
W·306 | → J21:2 | TB52:2→ | 24V Power | Field | 0V_LOGIC | TB52 |  | 2 | FERRULE | J21 |  | 2 | FERRULE | 18 | FALSE |  | 🟦⬜️ Blue/White
W·307 | → LS1 | TB51:3→ | 24V Power | Field | LIMIT_PWR | TB51 |  | 3 | FERRULE | LS1 |  |  |  |  | FALSE |  | 🟦 Blue
W·308 | → LS1 | TB52:3→ | 24V Power | Field | LIMIT_GND | TB52 |  | 3 | FERRULE | LS1 |  |  |  |  | FALSE |  | 🟦⬜️ Blue/White
W·309 | → LS2 | TB51:4→ | 24V Power | Field | LIMIT_PWR | TB51 |  | 4 | FERRULE | LS2 |  |  |  |  | FALSE |  | 🟦 Blue
W·310 | → LS2 | TB52:4→ | 24V Power | Field | LIMIT_GND | TB52 |  | 4 | FERRULE | LS2 |  |  |  |  | FALSE |  | 🟦⬜️ Blue/White
W·311 | → HS1 | TB51:5→ | 24V Power | Field | LIMIT_PWR | TB51 |  | 5 | FERRULE | HS1 |  |  |  |  | FALSE |  | 🟦 Blue
W·312 | → HS1 | TB52:5→ | 24V Power | Field | LIMIT_GND | TB52 |  | 5 | FERRULE | HS1 |  |  |  |  | FALSE |  | 🟦⬜️ Blue/White
W·313 | → HS2 | TB51:6→ | 24V Power | Field | LIMIT_PWR | TB51 |  | 6 | FERRULE | HS2 |  |  |  |  | FALSE |  | 🟦 Blue
W·314 | → HS2 | TB52:6→ | 24V Power | Field | LIMIT_GND | TB52 |  | 6 | FERRULE | HS2 |  |  |  |  | FALSE |  | 🟦⬜️ Blue/White
W·315 | → TP1 | TB51:7→ | 24V Power | Field | PROBE_PWR | TB51 |  | 7 | FERRULE | TP1 |  |  |  |  | FALSE |  | 🟦 Blue
W·317 | → P20:2 | P21:2→ | 24V Power | Field | 24V_LOGIC | P21 |  | 2 | FERRULE | P20 |  | 2 | FERRULE | 18 | TRUE |  | 🟦 Blue
W·318 | → P20:1 | P21:1→ | 24V Power | Field | 0V_LOGIC | P21 |  | 1 | FERRULE | P20 |  | 1 | FERRULE | 18 | TRUE |  | 🟦⬜️ Blue/White
W·319 | → TB53:1 | J20:2→ | 24V Power | Field | 24V_LOGIC | J20 |  | 2 | FERRULE | TB53 |  | 1 | FERRULE | 18 | FALSE |  | 🟦 Blue
W·320 | → TB54:1 | J20:1→ | 24V Power | Field | 0V_LOGIC | J20 |  | 1 | FERRULE | TB54 |  | 1 | FERRULE | 18 | FALSE |  | 🟦⬜️ Blue/White
W·321 | → J25:1 | TB53:2→ | 24V Power | Field | 24V_LOGIC | TB53 |  | 2 | FERRULE | J25 |  | 1 | FERRULE | 18 | FALSE |  | 🟦 Blue
W·322 | → J25:2 | TB54:2→ | 24V Power | Field | 0V_LOGIC | TB54 |  | 2 | FERRULE | J25 |  | 2 | FERRULE | 18 | FALSE |  | 🟦⬜️ Blue/White
W·323 | → LS3 | TB53:3→ | 24V Power | Field | LIMIT_PWR | TB53 |  | 3 | FERRULE | LS3 |  |  |  |  | FALSE |  | 🟦 Blue
W·324 | → LS3 | TB54:3→ | 24V Power | Field | LIMIT_GND | TB54 |  | 3 | FERRULE | LS3 |  |  |  |  | FALSE |  | 🟦⬜️ Blue/White
W·325 | → LS4 | TB53:4→ | 24V Power | Field | LIMIT_PWR | TB53 |  | 4 | FERRULE | LS4 |  |  |  |  | FALSE |  | 🟦 Blue
W·326 | → LS4 | TB54:4→ | 24V Power | Field | LIMIT_GND | TB54 |  | 4 | FERRULE | LS4 |  |  |  |  | FALSE |  | 🟦⬜️ Blue/White
W·327 | → HS3 | TB53:5→ | 24V Power | Field | LIMIT_PWR | TB53 |  | 5 | FERRULE | HS3 |  |  |  |  | FALSE |  | 🟦 Blue
W·328 | → HS3 | TB54:5→ | 24V Power | Field | LIMIT_GND | TB54 |  | 5 | FERRULE | HS3 |  |  |  |  | FALSE |  | 🟦⬜️ Blue/White
W·329 | → P29:2 | P25:2→ | 24V Power | Field | 24V_LOGIC | P25 |  | 2 | FERRULE | P29 |  | 2 | FERRULE | 18 | TRUE |  | 🟦 Blue
W·330 | → P29:1 | P25:1→ | 24V Power | Field | 0V_LOGIC | P25 |  | 1 | FERRULE | P29 |  | 1 | FERRULE | 18 | TRUE |  | 🟦⬜️ Blue/White
W·331 | → TB57:1 | J29:2→ | 24V Power | Field | 24V_LOGIC | J29 |  | 2 | FERRULE | TB57 |  | 1 | FERRULE | 18 | FALSE |  | 🟦 Blue
W·332 | → TB58:1 | J29:1→ | 24V Power | Field | 0V_LOGIC | J29 |  | 1 | FERRULE | TB58 |  | 1 | FERRULE | 18 | FALSE |  | 🟦⬜️ Blue/White
W·333 | → LS5 | TB57:2→ | 24V Power | Field | LIMIT_PWR | TB57 |  | 2 | FERRULE | LS5 |  |  |  |  | FALSE |  | 🟦 Blue
W·334 | → LS5 | TB58:2→ | 24V Power | Field | LIMIT_GND | TB58 |  | 2 | FERRULE | LS5 |  |  |  |  | FALSE |  | 🟦⬜️ Blue/White
W·335 | → LS6 | TB57:3→ | 24V Power | Field | LIMIT_PWR | TB57 |  | 3 | FERRULE | LS6 |  |  |  |  | FALSE |  | 🟦 Blue
W·336 | → LS6 | TB58:3→ | 24V Power | Field | LIMIT_GND | TB58 |  | 3 | FERRULE | LS6 |  |  |  |  | FALSE |  | 🟦⬜️ Blue/White
W·337 | → HS4 | TB57:4→ | 24V Power | Field | LIMIT_PWR | TB57 |  | 4 | FERRULE | HS4 |  |  |  |  | FALSE |  | 🟦 Blue
W·338 | → HS4 | TB58:4→ | 24V Power | Field | LIMIT_GND | TB58 |  | 4 | FERRULE | HS4 |  |  |  |  | FALSE |  | 🟦⬜️ Blue/White
W·391 | → K2 | P4:1→ | 24V Power | Field | 24V_LOGIC | P4 |  | 1 | FERRULE | K2 |  |  |  | 18 | FALSE |  | 🟦 Blue | Need suitable relay
W·392 | → K2 | P4:2→ | 24V Power | Field | 0V_LOGIC | P4 |  | 2 | FERRULE | K2 |  |  |  | 18 | FALSE |  | 🟦⬜️ Blue/White | Need suitable relay
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

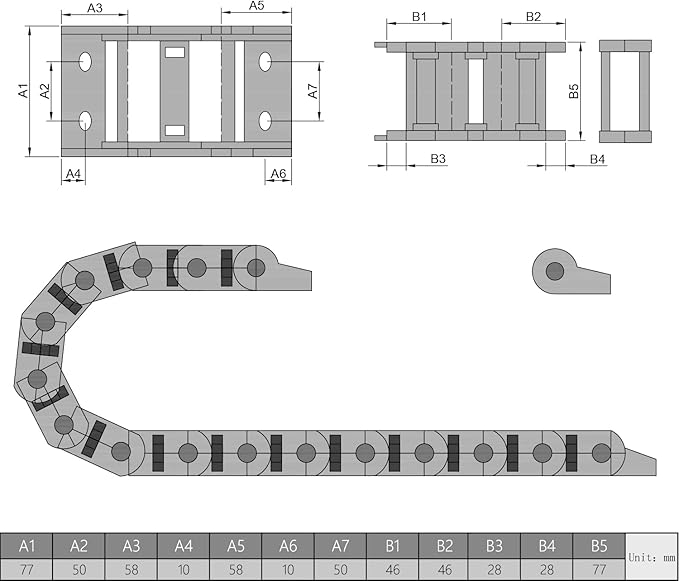
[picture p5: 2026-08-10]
documentation/wiring-diagram/components/Drag Chain Drawing 1.jpg

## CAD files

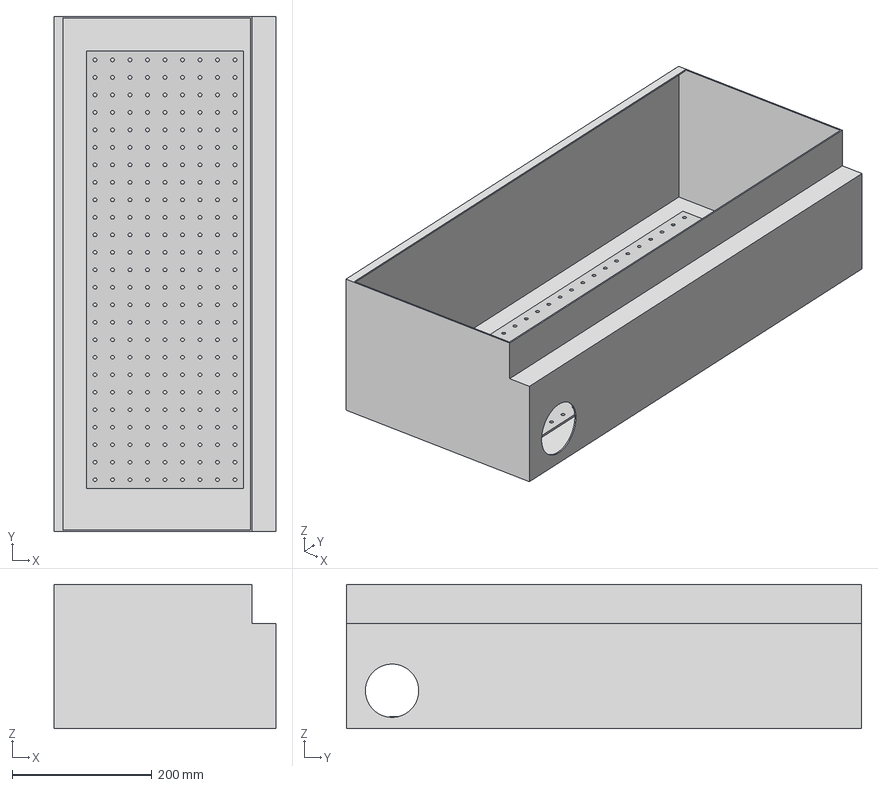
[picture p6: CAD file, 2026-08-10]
cad/controller/Square D Cabinet Assembly v2.step
317.0 x 736.0 x 206.0 mm
Cabinet Base
Square D Internal Mounting Plate

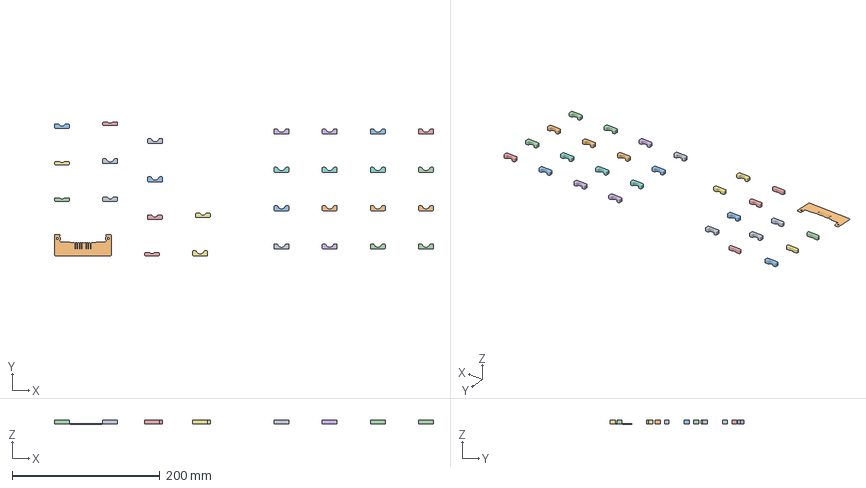
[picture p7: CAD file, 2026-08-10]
cad/cabinet/Flexible Inserts v01.3mf
513.8 x 181.3 x 6.00 mm
Strain Relief Inserts v2.stl x 25
Dust Guard v5.stl
Strain Relief Inserts v2.stl_2
Strain Relief Inserts v2.stl_3
Strain Relief Inserts v2.stl_1

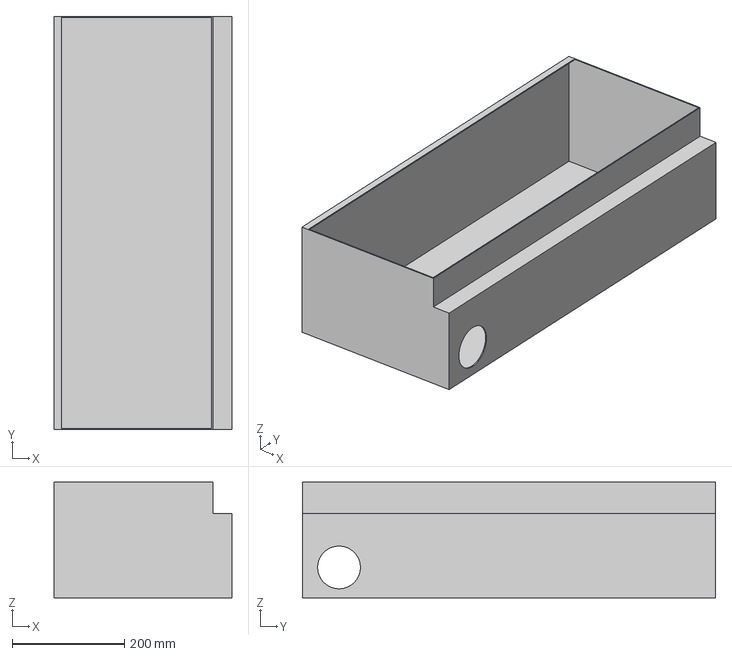
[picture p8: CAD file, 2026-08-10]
cad/controller/Square D Cabinet v1.step
317.0 x 736.0 x 206.0 mm

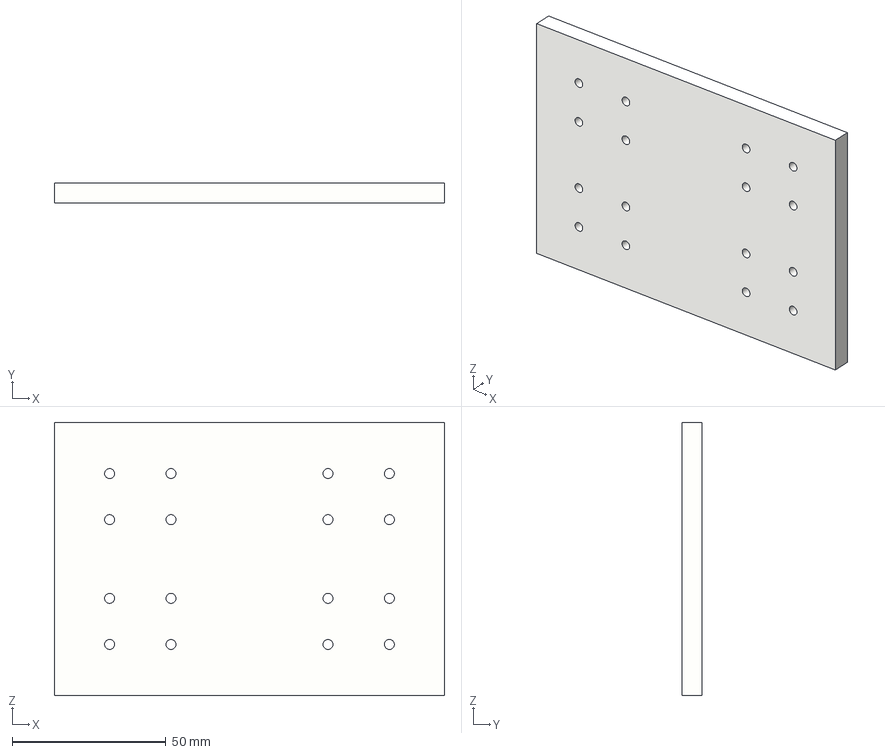
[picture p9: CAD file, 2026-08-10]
cad/din mounts/Z Spindle Mount Plate imp.step
127.0 x 6.50 x 88.9 mm

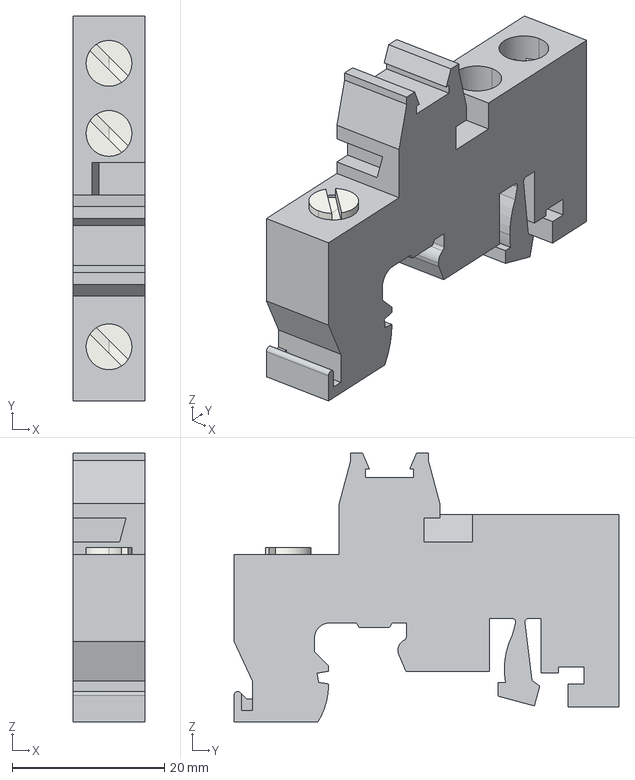
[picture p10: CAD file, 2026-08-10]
cad/power/E-UK - End bracket 1201442.stp
9.50 x 50.5 x 35.3 mm

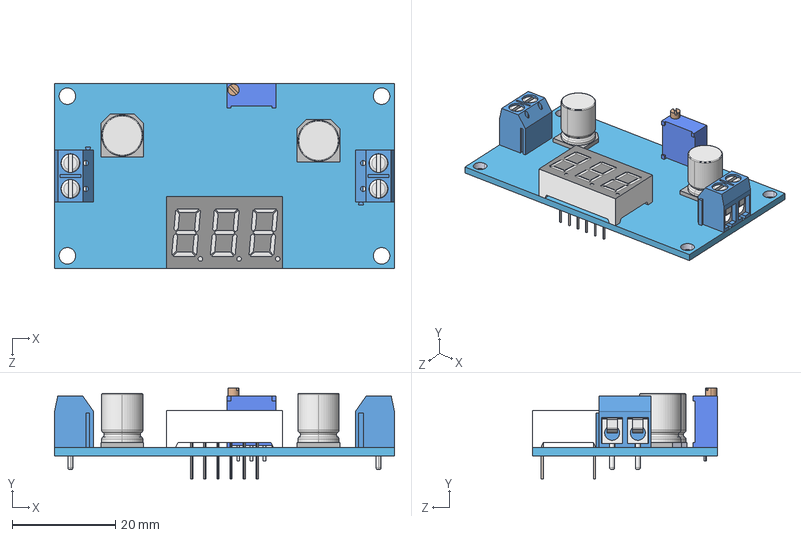
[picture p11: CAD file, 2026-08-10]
cad/power/lm2596-buck-converter-4-0-40-to-1-3-37v-adjustable-step-down-power-module-with-led-display-volt-meter-1/LM2596 Buck Converter 4.0-40 to 1.3-37V.STEP
66.0 x 17.6 x 36.0 mm
Base, LM2596 Buck Converter 4.0-40 to 1.3-37V
DG301-5.0-02, LM2596 Buck Converter 4.0-40 to 1.3-37V x 2
3 Digit 7 Segment Display, LM2596 Buck Converter 4.0-40 to 1.3-37V
Trimpot 3296W, LM2596 Buck Converter 4.0-40 to 1.3-37V_Valor predeterminado
220 35V Capacitor, LM2596 Buck Converter 4.0-40 to 1.3-37V x 2

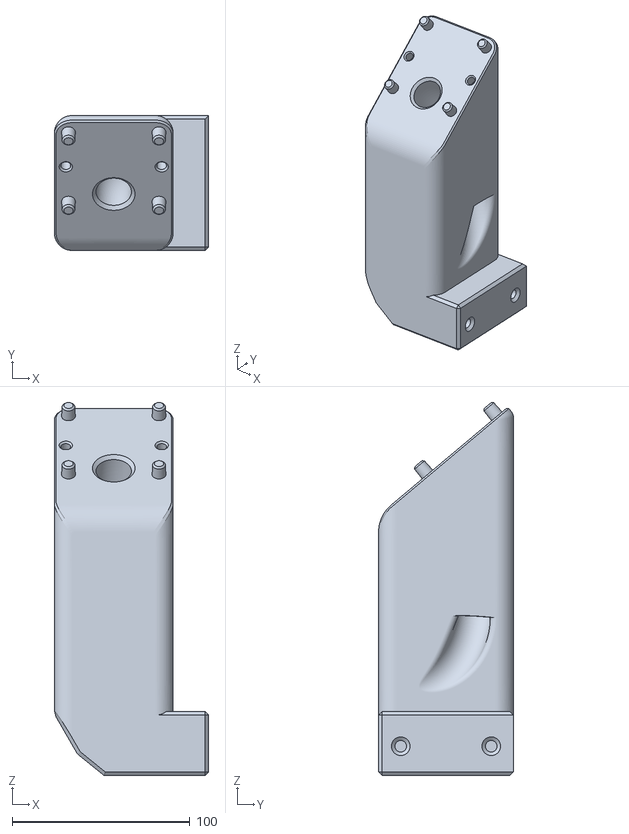
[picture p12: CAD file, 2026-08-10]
cad/support files/E-Stop Mount.stl
87.0 x 76.0 x 210.1

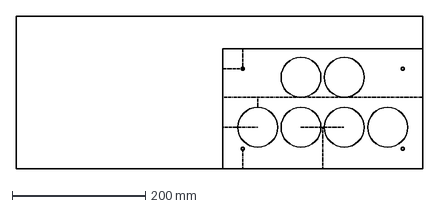
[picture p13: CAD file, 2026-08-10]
documentation/wiring-diagram/reference/Breakout Box Hole Pattern.dxf
609.6 x 228.6 mm

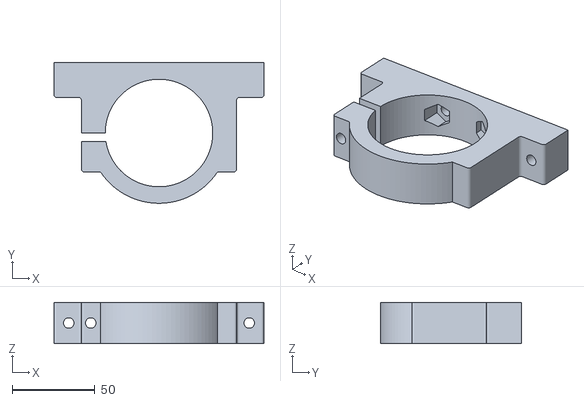
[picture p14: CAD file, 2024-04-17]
Spindle Mount/Dusty Spindle Mount.stl
127.0 x 85.0 x 25.0

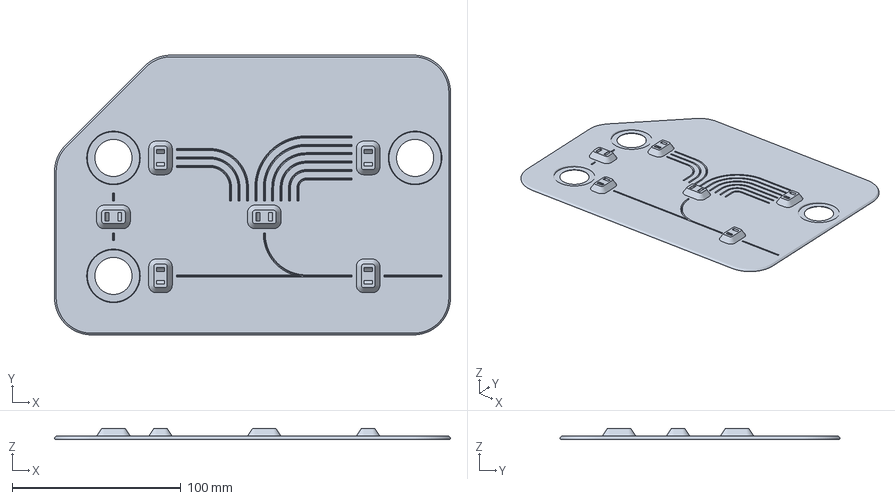
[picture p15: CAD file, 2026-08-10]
cad/cabinet/Door Interior Cable Management Panel.3mf
235.0 x 166.0 x 6.50 mm

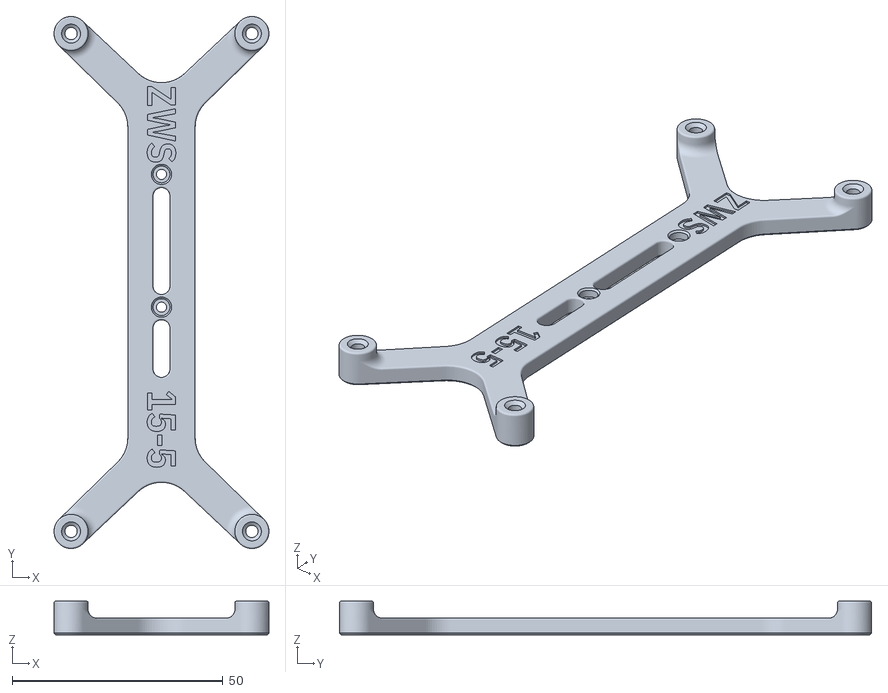
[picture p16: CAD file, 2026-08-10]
cad/din mounts/ZWS15-5 Din Rail Mount.stl
51.0 x 126.2 x 8.00

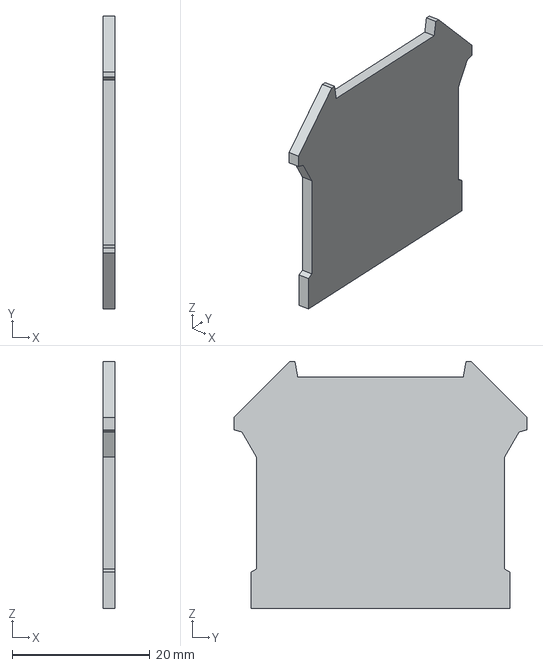
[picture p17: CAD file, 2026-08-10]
cad/power/D-UK 4-10 - End cover 3003020.stp
1.80 x 42.5 x 35.9 mm

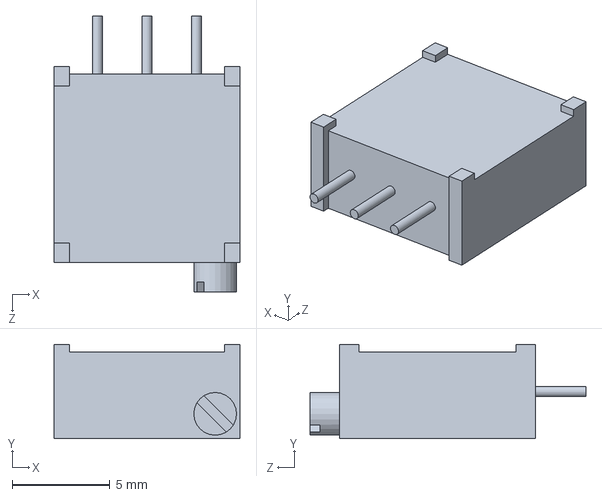
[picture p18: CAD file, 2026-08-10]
cad/power/lm2596-buck-converter-4-0-40-to-1-3-37v-adjustable-step-down-power-module-with-led-display-volt-meter-1/Trimpot 3296W, LM2596 Buck Converter 4.0-40 to 1.3-37V.SLDPRT
9.53 x 4.83 x 14.1 mm

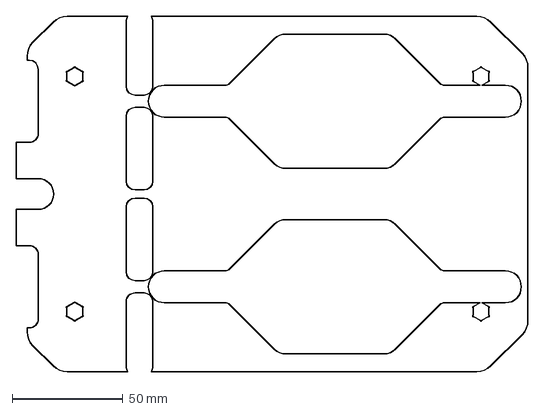
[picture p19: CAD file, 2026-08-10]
cad/support files/DB Case Base.dxf
231.2 x 160.6 mm

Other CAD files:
documentation/wiring-diagram/reference/Cabinet Bottom Panel Hole Pattern.dxf
Spindle Mount/Dusty Z Motor Mount.stl
cad/cabinet/Breakout Box v01.3mf
cad/din mounts/Duet3_Mini_5_+expander DIN Mounts.step
Spindle Mount/Spindle Mount v54.f3d
cad/din mounts/50mm DIN Rail Bracket.step
cad/din mounts/DIN Clip.step
cad/din mounts/DIN Clip.stl
cad/power/171460759-659-1757019/1757019.stp
cad/power/171460764-659-1786190/1786190.stp
cad/power/171460776-659-1757035/1757035.stp
cad/power/171460777-659-1786239/1786239.stp
cad/power/171460780-659-1757077/1757077.stp
cad/power/171460794-659-1786174/1786174.stp
cad/power/171461315-659-1689750/1689750.stp
cad/power/171492348-659-1727078/1727078.stp
cad/power/171497401-659-3273290/3273290.stp
cad/power/171497408-659-3273268/3273268.stp
cad/power/171497412-659-3273278/3273278.stp
cad/power/171497421-659-3273300/3273300.stp
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

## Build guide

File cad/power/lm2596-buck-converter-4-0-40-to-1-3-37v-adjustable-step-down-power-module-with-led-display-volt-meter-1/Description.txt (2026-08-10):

LM2596 Buck Converter 4.0~40 to 1.3-37V Adjustable Step-Down Power Module with LED Display Volt meter

Link to CAD file:
https://grabcad.com/library/lm2596-buck-converter-4-0-40-to-1-3-37v-adjustable-step-down-power-module-with-led-display-volt-meter-1

#CAD #SolidWorks #3dmodel #buckconverter #stepdownbuckconverter #LM2596

Input voltage:4.0V-40V

Output voltage:1.25V～37V

Voltage regulation ± 2.5%

Switching frequency:150KHz

Conversion efficiency: 92%(highest),
Load regulation ±0.5%

Max Electric current: 3A
Normal working electric current: 2A

150KHz Internal oscillation frequency
Low power consumption
High efficiency

Buy Links:
https://www.aliexpress.us/item/2251832392854599.html

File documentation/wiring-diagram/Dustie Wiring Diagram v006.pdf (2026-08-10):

# Cabinet Temperature Sensor

Will be using for fan speed control and safety shutdown. Need input on how to set this up.

From the Mesa manual:

ANALOG INPUTS
Four field input pins are capable of reading the input voltage. These are not highly accurate or high resolution but can be useful for things like potentiometer inputs. Input resolution is 8 bits and input full scale value is 36.3V. Accuracy is +-5%. Software process data modes 1 and 2 allow reading the analog voltage on inputs 0 through 3, in addition to the 32 digital bit inputs.

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
### 1 L1

### 3 L2

### 5 L3

### 13 NO

### 21 NC

A1

### 2 T1

### 4 T2

### 6 T3

### 14 NO

### 22 NC

A2

K1

MCB

# STOP

# EMERGENCY

NO | NC

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
Cabinet Estop

PS1

101

102

1

2

EMI Filter

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
Terminal Block TB1

Terminal Block TB2

Terminal Block TB3

Terminal Block TB5

# VFD1

# GX16 (2P)

J7 - P7

911

# GX16 (4P)

J8 - P8

25
26
910

PS2

907

9

10

Terminal Block TB4

Q1 F1

PS3

7

8

Terminal Block TB11 | 207

201

202

SD1

# GX16 (4P)

J5 - P5

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
# GX16 (2P)

J6 - P6

# GX16 (2P)

J4 - P4

# GX16 (2P)

J3 - P3

# GX16 (2P)

J2 - P2

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
# DB25-M

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
# MESA

# HDMI Extension

# USB Extension

# WiFi Extension

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
# DB25-F

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
# Touch PlateTP1

# GX16 (4P)

P13 - J13

# GX16 (2P)

P12 - J12

# GX16 (2P)

P11 - J11

# GX16 (2P)

P10 - J10

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
# GX16 (4P)

J18 - P18

# GX16 (2P)

J17 - P17

# GX16 (2P)

J16 - P16

# GX16 (2P)

J15 - P15

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
TB51

TB52

# DB25-F

J9

# DB25-M

P9

# DB25-M

J14

# Static Platform

# CNC Table Breakout Box 1

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
# DB25-F

P14

# DB25-M

P19

X−
LS3

X+
LS4

X
HS3

# GX16 (4P)

P23 - J23

# GX16 (2P)

P22 - J22

# GX16 (2P)

P21 - J21

# GX16 (2P)

P20 - J20

# Y Platform

# Gantry Breakout Box 2

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
# Integrated Stepper Y2

IM2

629

630

631

# DB25-F

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
# Integrated Stepper Y1

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
TB57

TB58

# GX16 (4P)

P31 - J31

# GX16 (2P)

P30 - J30

# GX16 (2P)

P29 - J29

# X Platform

# Toolhead Breakout Box 3

638

639

640

243

244 | 245
| 247
| 249

246
248
250

596
595
594
593

# Integrated Stepper X

IM3

333

334

# GX16 (4P)

J27 - P27

# GX16 (2P)

J26 - P26

# GX16 (2P)

J25 - P25

515

# Stepper Z

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
J24 | P24 | P28 | J28

# Control Cabinet Wall Mounted

TB53

TB54

TB55

TB56

# Coolant Pump Relay

K2

Terminal Block TB6

Terminal Block TB10

Terminal Block TB8

Terminal Block TB9

Terminal Block TB7

160
161
162

# GX16 (4P)

J30 - P30

# GX16 (4P)

J29 - P29

112 | 113

151
152
153

108

154

115

# STOP

# EMERGENCY

NO | NC
PL2 | S2

159

116

106

117

Static Platform
Estop

# MPG

# Manual Pulse Generator

# STOP

# EMERGENCY

NO | NC

S3
PL3

176

MPG Estop

water

water

# Spindle

M1

# GX16 (4P)

P31 - J31

# GX16 (4P)

P32 - J32

# GX16 (4P)

P33 - J33

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
# GX16 (4P)

P34 - J34

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
Fan Control
- Mosfet?

10kΩ NTC Thermistor

(?)Ω R

# Cabinet Air Intake Fan Control

Will use fans with a pre-filter to maintain positive pressure in cabinet (for dust control) and temperature regulation. Need input on how to set this up.

- 4 120mm Fans specified
- VHS has 2 24v, and ∞ 12V models
- is 2x24V + 2x12V or 4x12V better?
- 12V powered via buck converter presumably okay?
- Need to run 100% if no control signal (e.g. failsafe and boot states)
- Able to modulate based on temperature (MOSFET control circuit via Mesa?)

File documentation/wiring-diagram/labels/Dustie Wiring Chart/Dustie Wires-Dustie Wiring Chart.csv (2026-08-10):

Wire | Label From | Wire From | Label To | Wire To | Zone | Location | Signal | From Device | From Mesa TB | From Terminal | From Type | To Device | To Mesa TB | To Terminal | To Type | AWG | Flex | Length | Colour | Notes
W-001 | W-001 · AC_L1_IN ⇒TB1:5 | ⇒TB1:5 | W-001 · AC_L1_IN P0:L1⇒ | P0:L1⇒ | 240V Power | Main Cabinet | ac_l1_in | P0 |  | L1 | Other | TB1 |  | 5 | Ferrule | 10 | FALSE |  | 🟥 Red
W-002 | W-002 · AC_L2_IN ⇒TB1:3 | ⇒TB1:3 | W-002 · AC_L2_IN P0:L2⇒ | P0:L2⇒ | 240V Power | Main Cabinet | AC_L2_IN | P0 |  | L2 | Other | TB1 |  | 3 | Ferrule | 10 | FALSE |  | ⬛️ Black
W-003 | W-003 · AC_L1_IN ⇒Q1:1 | ⇒Q1:1 | W-003 · AC_L1_IN TB1:6⇒ | TB1:6⇒ | 240V Power | Main Cabinet | ac_l1_in | TB1 |  | 6 | Ferrule | Q1 |  | 1 | Ferrule | 10 | FALSE |  | 🟥 Red
W-004 | W-004 · AC_L2_IN ⇒Q1:3 | ⇒Q1:3 | W-004 · AC_L2_IN TB1:4⇒ | TB1:4⇒ | 240V Power | Main Cabinet | AC_L2_IN | TB1 |  | 4 | Ferrule | Q1 |  | 3 | Ferrule | 10 | FALSE |  | ⬛️ Black
W-005 | W-005 · AC_L1_FUSED ⇒F1:1 | ⇒F1:1 | W-005 · AC_L1_FUSED Q1:2⇒ | Q1:2⇒ | 240V Power | Main Cabinet | ac_l1_fused | Q1 |  | 2 | Ferrule | F1 |  | 1 | Ring | 10 | FALSE |  | 🟥 Red
W-006 | W-006 · AC_L2_FUSED ⇒F1:2 | ⇒F1:2 | W-006 · AC_L2_FUSED Q1:4⇒ | Q1:4⇒ | 240V Power | Main Cabinet | AC_l2_fused | Q1 |  | 4 | Ferrule | F1 |  | 2 | Ring | 10 | FALSE |  | ⬛️ Black
W-007 | W-007 · AC_L1_FILTERED ⇒TB2:1 | ⇒TB2:1 | W-007 · AC_L1_FILTERED F1:3⇒ | F1:3⇒ | 240V Power | Main Cabinet | AC_l1_filtered | F1 |  | 3 | Ring | TB2 |  | 1 | Ferrule | 10 | FALSE |  | 🟥 Red
W-008 | W-008 · AC_L2_FILTERED ⇒TB2:11 | ⇒TB2:11 | W-008 · AC_L2_FILTERED F1:4⇒ | F1:4⇒ | 240V Power | Main Cabinet | AC_l2_filtered | F1 |  | 4 | Ring | TB2 |  | 11 | Ferrule | 10 | FALSE |  | ⬛️ Black
W-009 | W-009 · AC_L1_FILTERED ⇒PS1:L | ⇒PS1:L | W-009 · AC_L1_FILTERED TB2:10⇒ | TB2:10⇒ | 240V Power | Main Cabinet | AC_l1_filtered | TB2 |  | 10 | Ferrule | PS1 |  | L | Ferrule | 14 | FALSE |  | 🟥 Red
W-010 | W-010 · AC_L2_FILTERED ⇒PS1:N | ⇒PS1:N | W-010 · AC_L2_FILTERED TB2:20⇒ | TB2:20⇒ | 240V Power | Main Cabinet | AC_l2_filtered | TB2 |  | 20 | Ferrule | PS1 |  | N | Ferrule | 14 | FALSE |  | ⬛️ Black
W-011 | W-011 · AC_L1_FILTERED ⇒K1:L1 | ⇒K1:L1 | W-011 · AC_L1_FILTERED TB2:8⇒ | TB2:8⇒ | 240V Power | Main Cabinet | AC_l1_filtered | TB2 |  | 8 | Ferrule | K1 |  | L1 | Ring | 10 | FALSE |  | 🟥 Red
W-012 | W-012 · AC_L2_FILTERED ⇒K1:L2 | ⇒K1:L2 | W-012 · AC_L2_FILTERED TB2:18⇒ | TB2:18⇒ | 240V Power | Main Cabinet | AC_l2_filtered | TB2 |  | 18 | Ferrule | K1 |  | L2 | Ring | 10 | FALSE |  | ⬛️ Black
W-013 | W-013 · AC_L1_FILTERED ⇒PS2:L | ⇒PS2:L | W-013 · AC_L1_FILTERED TB2:6⇒ | TB2:6⇒ | 240V Power | Main Cabinet | AC_l1_filtered | TB2 |  | 6 | Ferrule | PS2 |  | L | Other | 10 | FALSE |  | 🟥 Red
W-014 | W-014 · AC_L2_FILTERED ⇒PS2:N | ⇒PS2:N | W-014 · AC_L2_FILTERED TB2:16⇒ | TB2:16⇒ | 240V Power | Main Cabinet | AC_l2_filtered | TB2 |  | 16 | Ferrule | PS2 |  | N | Other | 10 | FALSE |  | ⬛️ Black
W-015 | W-015 · AC_L1_FILTERED ⇒J35:L | ⇒J35:L | W-015 · AC_L1_FILTERED TB2:4⇒ | TB2:4⇒ | 240V Power | Main Cabinet | AC_l1_filtered | TB2 |  | 4 | Ferrule | J35 |  | L | Solder | 10 | FALSE |  | 🟥 Red
W-016 | W-016 · AC_L2_FILTERED ⇒J35:N | ⇒J35:N | W-016 · AC_L2_FILTERED TB2:14⇒ | TB2:14⇒ | 240V Power | Main Cabinet | AC_l2_filtered | TB2 |  | 14 | Ferrule | J35 |  | N | Solder | 10 | FALSE |  | ⬛️ Black
W-021 | W-021 · AC_L1_FILTERED ⇒TB3:1 | ⇒TB3:1 | W-021 · AC_L1_FILTERED K1:T1⇒ | K1:T1⇒ | 240V Power | Main Cabinet | AC_l1_filtered | K1 |  | T1 | Ring | TB3 |  | 1 | Ferrule | 10 | FALSE |  | 🟥 Red
W-022 | W-022 · AC_L2_FILTERED ⇒TB3:11 | ⇒TB3:11 | W-022 · AC_L2_FILTERED K1:T2⇒ | K1:T2⇒ | 240V Power | Main Cabinet | AC_l2_filtered | K1 |  | T2 | Ring | TB3 |  | 11 | Ferrule | 10 | FALSE |  | ⬛️ Black
W-023 | W-023 · AC_L1_FILTERED ⇒PS5:L | ⇒PS5:L | W-023 · AC_L1_FILTERED TB3:10⇒ | TB3:10⇒ | 240V Power | Main Cabinet | AC_l1_filtered | TB3 |  | 10 | Ferrule | PS5 |  | L | Ring | 10 | FALSE |  | 🟥 Red
W-024 | W-024 · AC_L2_FILTERED ⇒PS5:N | ⇒PS5:N | W-024 · AC_L2_FILTERED TB3:20⇒ | TB3:20⇒ | 240V Power | Main Cabinet | AC_l2_filtered | TB3 |  | 20 | Ferrule | PS5 |  | N | Ring | 10 | FALSE |  | ⬛️ Black
W-025 | W-025 · AC_L1_FILTERED ⇒PS6:L | ⇒PS6:L | W-025 · AC_L1_FILTERED TB3:8⇒ | TB3:8⇒ | 240V Power | Main Cabinet | AC_l1_filtered | TB3 |  | 8 | Ferrule | PS6 |  | L | Ring | 10 | FALSE |  | 🟥 Red
W-026 | W-026 · AC_L2_FILTERED ⇒PS6:N | ⇒PS6:N | W-026 · AC_L2_FILTERED TB3:18⇒ | TB3:18⇒ | 240V Power | Main Cabinet | AC_l2_filtered | TB3 |  | 18 | Ferrule | PS6 |  | N | Ring | 10 | FALSE |  | ⬛️ Black
W-027 | W-027 · AC_L1_FILTERED ⇒PS4:L | ⇒PS4:L | W-027 · AC_L1_FILTERED TB3:6⇒ | TB3:6⇒ | 240V Power | Main Cabinet | AC_l1_filtered | TB3 |  | 6 | Ferrule | PS4 |  | L | Ferrule | 10 | FALSE |  | 🟥 Red
W-028 | W-028 · AC_L2_FILTERED ⇒PS4:N | ⇒PS4:N | W-028 · AC_L2_FILTERED TB3:16⇒ | TB3:16⇒ | 240V Power | Main Cabinet | AC_l2_filtered | TB3 |  | 16 | Ferrule | PS4 |  | N | Ferrule | 10 | FALSE |  | ⬛️ Black
W-029 | W-029 · AC_L1_FILTERED ⇒J6:4 | ⇒J6:4 | W-029 · AC_L1_FILTERED TB3:4⇒ | TB3:4⇒ | 240V Power | Main Cabinet | AC_l1_filtered | TB3 |  | 4 | Ferrule | J6 |  | 4 | Ferrule | 10 | FALSE |  | 🟥 Red
W-030 | W-030 · AC_L2_FILTERED ⇒J6:3 | ⇒J6:3 | W-030 · AC_L2_FILTERED TB3:14⇒ | TB3:14⇒ | 240V Power | Main Cabinet | AC_l2_filtered | TB3 |  | 14 | Ferrule | J6 |  | 3 | Ferrule | 10 | FALSE |  | ⬛️ Black
W-051 | W-051 · AC_L1_FILTERED ⇒VFD1:R | ⇒VFD1:R | W-051 · AC_L1_FILTERED P6:4⇒ | P6:4⇒ | 240V Power | Field | AC_l1_filtered | P6 |  | 4 | Ferrule | VFD1 |  | R | Ferrule | 10 | FALSE |  | 🟥 Red | Check GX Contact Numbering
W-052 | W-052 · AC_L2_FILTERED ⇒VFD1:S | ⇒VFD1:S | W-052 · AC_L2_FILTERED P6:3⇒ | P6:3⇒ | 240V Power | Field | AC_l2_filtered | P6 |  | 3 | Ferrule | VFD1 |  | S | Ferrule | 10 | FALSE |  | ⬛️ Black | Check GX Contact Numbering
W-053 | W-053 · AC_L1_FILTERED ⇒J36:L | ⇒J36:L | W-053 · AC_L1_FILTERED P35:L⇒ | P35:L⇒ | 240V Power | Field | AC_l1_filtered | P35 |  | L | Other | J36 |  | L | Other | 14 | FALSE |  | 🟥 Red
W-054 | W-054 · AC_L2_FILTERED ⇒J36:N | ⇒J36:N | W-054 · AC_L2_FILTERED P35:N⇒ | P35:N⇒ | 240V Power | Field | AC_l2_filtered | P35 |  | N | Other | J36 |  | N | Other | 14 | FALSE |  | ⬛️ Black
W-101 | W-101 · 24V_LOGIC ⇒TB5:1 | ⇒TB5:1 | W-101 · 24V_LOGIC PS1:V＋⇒ | PS1:V＋⇒ | Estop/Power Mgmt | Main Cabinet | 24V_LOGIC | PS1 |  | V＋ | Ferrule | TB5 |  | 1 | Ferrule | 14 | FALSE |  | 🟦 Blue
W-102 | W-102 · 0V_LOGIC ⇒TB5:9 | ⇒TB5:9 | W-102 · 0V_LOGIC PS1:V－⇒ | PS1:V－⇒ | Estop/Power Mgmt | Main Cabinet | 0V_Logic | PS1 |  | V－ | Ferrule | TB5 |  | 9 | Ferrule | 14 | FALSE |  | 🟦⬜️ Blue/White
W-103 | W-103 · 24V_LOGIC ⇒S1:21 | ⇒S1:21 | W-103 · 24V_LOGIC TB5:8⇒ | TB5:8⇒ | Estop/Power Mgmt | Main Cabinet | 24V_LOGIC | TB5 |  | 8 | Ferrule | S1 |  | 21 | Ferrule | 14 | FALSE |  | 🟦 Blue
W-104 | W-104 · 24V_LOGIC ⇒S1:13 | ⇒S1:13 | W-104 · 24V_LOGIC TB5:6⇒ | TB5:6⇒ | Estop/Power Mgmt | Main Cabinet | 24V_LOGIC | TB5 |  | 6 | Ferrule | S1 |  | 13 | Ferrule | 14 | FALSE |  | 🟦 Blue
W-105 | W-105 · 24V_LOGIC ⇒J7:7 | ⇒J7:7 | W-105 · 24V_LOGIC TB5:4⇒ | TB5:4⇒ | Estop/Power Mgmt | Main Cabinet | 24V_LOGIC | TB5 |  | 4 | Ferrule | J7 |  | 7 | Ferrule | 14 | FALSE |  | 🟦 Blue
W-106 | W-106 · 24V_LOGIC ⇒J7:3 | ⇒J7:3 | W-106 · 24V_LOGIC TB5:2⇒ | TB5:2⇒ | Estop/Power Mgmt | Main Cabinet | 24V_LOGIC | TB5 |  | 2 | Ferrule | J7 |  | 3 | Ferrule | 14 | FALSE |  | 🟦 Blue
W-107 | W-107 · ESTOP_INDICATOR ⇒PL1:X1 | ⇒PL1:X1 | W-107 · ESTOP_INDICATOR TB5:18⇒ | TB5:18⇒ | Estop/Power Mgmt | Main Cabinet | Estop_indicator | TB5 |  | 18 | Ferrule | PL1 |  | X1 | Ferrule | 14 | FALSE |  | 🟦⬜️ Blue/White
W-108 | W-108 · ESTOP_INDICATOR ⇒J7:6 | ⇒J7:6 | W-108 · ESTOP_INDICATOR TB5:16⇒ | TB5:16⇒ | Estop/Power Mgmt | Main Cabinet | Estop_indicator | TB5 |  | 16 | Ferrule | J7 |  | 6 | Ferrule | 14 | FALSE |  | 🟦⬜️ Blue/White
W-109 | W-109 · ESTOP_INDICATOR ⇒J7:2 | ⇒J7:2 | W-109 · ESTOP_INDICATOR TB5:14⇒ | TB5:14⇒ | Estop/Power Mgmt | Main Cabinet | Estop_indicator | TB5 |  | 14 | Ferrule | J7 |  | 2 | Ferrule | 14 | FALSE |  | 🟦⬜️ Blue/White
W-110 | W-110 · 0V_LOGIC ⇒PL4:X2 | ⇒PL4:X2 | W-110 · 0V_LOGIC TB5:12⇒ | TB5:12⇒ | Estop/Power Mgmt | Main Cabinet | 0V_Logic | TB5 |  | 12 | Ferrule | PL4 |  | X2 | Ferrule | 14 | FALSE |  | 🟦⬜️ Blue/White
W-111 | W-111 · 0V_LOGIC ⇒A2 | ⇒A2 | W-111 · 0V_LOGIC TB5:10⇒ | TB5:10⇒ | Estop/Power Mgmt | Main Cabinet | 0V_Logic | TB5 |  | 10 | Ferrule |  |  | A2 | Ferrule | 14 | FALSE |  | 🟦⬜️ Blue/White
W-112 | W-112 · ESTOP_LOOP ⇒TB8:1 | ⇒TB8:1 | W-112 · ESTOP_LOOP S1:22⇒ | S1:22⇒ | Estop/Power Mgmt | Main Cabinet | Estop_loop | S1 |  | 22 | Ferrule | tb8 |  | 1 | Ferrule | 14 | FALSE |  | 🟦 Blue
W-113 | W-113 · ESTOP_LOOP ⇒J7:8 | ⇒J7:8 | W-113 · ESTOP_LOOP TB8:2⇒ | TB8:2⇒ | Estop/Power Mgmt | Main Cabinet | Estop_loop | TB8 |  | 2 | Ferrule | J7 |  | 8 | Ferrule | 14 | FALSE |  | 🟦 Blue
W-114 | W-114 · 24V_LOGIC ⇒PL1:X2 | ⇒PL1:X2 | W-114 · 24V_LOGIC S1:14⇒ | S1:14⇒ | Estop/Power Mgmt | Main Cabinet | 24V_LOGIC | S1 |  | 14 | Ferrule | PL1 |  | X2 | Ferrule | 14 | FALSE |  | 🟦 Blue
W-115 | W-115 · ESTOP_LOOP ⇒TB9:1 | ⇒TB9:1 | W-115 · ESTOP_LOOP J7:5⇒ | J7:5⇒ | Estop/Power Mgmt | Main Cabinet | Estop_loop | J7 |  | 5 | Ferrule | TB9 |  | 1 | Ferrule | 14 | FALSE |  | 🟦 Blue
W-116 | W-116 · ESTOP_LOOP ⇒J7:4 | ⇒J7:4 | W-116 · ESTOP_LOOP TB9:2⇒ | TB9:2⇒ | Estop/Power Mgmt | Main Cabinet | Estop_loop | TB9 |  | 2 | Ferrule | J7 |  | 4 | Ferrule | 14 | FALSE |  | 🟦 Blue
W-117 | W-117 · ESTOP_LOOP ⇒TB10:1 | ⇒TB10:1 | W-117 · ESTOP_LOOP J7:1⇒ | J7:1⇒ | Estop/Power Mgmt | Main Cabinet | Estop_loop | J7 |  | 1 | Ferrule | TB10 |  | 1 | Ferrule | 14 | FALSE |  | 🟦 Blue
W-118 | W-118 · ESTOP_LOOP ⇒PB2:21 | ⇒PB2:21 | W-118 · ESTOP_LOOP TB10:2⇒ | TB10:2⇒ | Estop/Power Mgmt | Main Cabinet | Estop_loop | TB10 |  | 2 | Ferrule | PB2 |  | 21 | Ferrule | 14 | FALSE |  | 🟦 Blue
W-119 | W-119 · ESTOP_LOOP ⇒TB6:1 | ⇒TB6:1 | W-119 · ESTOP_LOOP PB2:22⇒ | PB2:22⇒ | Estop/Power Mgmt | Main Cabinet | Estop_loop | PB2 |  | 22 | Ferrule | TB6 |  | 1 | Ferrule | 14 | FALSE |  | 🟦 Blue
W-120 | W-120 · ESTOP_LOOP ⇒PB1:13 | ⇒PB1:13 | W-120 · ESTOP_LOOP TB6:2⇒ | TB6:2⇒ | Estop/Power Mgmt | Main Cabinet | Estop_loop | TB6 |  | 2 | Ferrule | PB1 |  | 13 | Ferrule | 14 | FALSE |  | 🟦 Blue
W-121 | W-121 · ESTOP_LOOP ⇒K1:13 | ⇒K1:13 | W-121 · ESTOP_LOOP TB6:4⇒ | TB6:4⇒ | Estop/Power Mgmt | Main Cabinet | Estop_loop | TB6 |  | 4 | Ferrule | K1 |  | 13 | Ferrule | 14 | FALSE |  | 🟦 Blue
W-122 | W-122 · MACHINE_ENABLE ⇒TB7:1 | ⇒TB7:1 | W-122 · MACHINE_ENABLE PB1:14⇒ | PB1:14⇒ | Estop/Power Mgmt | Main Cabinet | Machine_enable | PB1 |  | 14 | Ferrule | TB7 |  | 1 | Ferrule | 14 | FALSE |  | 🟦 Blue
W-123 | W-123 · MACHINE_ENABLE ⇒K1:14 | ⇒K1:14 | W-123 · MACHINE_ENABLE TB7:4⇒ | TB7:4⇒ | Estop/Power Mgmt | Main Cabinet | Machine_enable | TB7 |  | 4 | Ferrule | K1 |  | 14 | Ferrule | 14 | FALSE |  | 🟦 Blue
W-124 | W-124 · MACHINE_ENABLE ⇒K1:A1 | ⇒K1:A1 | W-124 · MACHINE_ENABLE TB7:6⇒ | TB7:6⇒ | Estop/Power Mgmt | Main Cabinet | Machine_enable | TB7 |  | 6 | Ferrule | K1 |  | A1 | Ferrule | 14 | FALSE |  | 🟦 Blue
W-125 | W-125 · MACHINE_ENABLE ⇒PL4:X1 | ⇒PL4:X1 | W-125 · MACHINE_ENABLE TB7:2⇒ | TB7:2⇒ | Estop/Power Mgmt | Main Cabinet | Machine_enable | TB7 |  | 2 | Ferrule | PL4 |  | X1 | Ferrule | 14 | FALSE |  | 🟦 Blue
W-151 | W-151 · ESTOP_LOOP ⇒P12:8 | ⇒P12:8 | W-151 · ESTOP_LOOP P7:8⇒ | P7:8⇒ | Estop/Power Mgmt | Field | Estop_loop | P7 |  | 8 | Ferrule | P12 |  | 8 | Ferrule | 14 | FALSE |  | 🟦 Blue
W-152 | W-152 · 24V_LOGIC ⇒P12:7 | ⇒P12:7 | W-152 · 24V_LOGIC P7:7⇒ | P7:7⇒ | Estop/Power Mgmt | Field | 24V_LOGIC | P7 |  | 7 | Ferrule | P12 |  | 7 | Ferrule | 14 | FALSE |  | 🟦 Blue
W-153 | W-153 · ESTOP_INDICATOR ⇒P12:6 | ⇒P12:6 | W-153 · ESTOP_INDICATOR P7:6⇒ | P7:6⇒ | Estop/Power Mgmt | Field | Estop_indicator | P7 |  | 6 | Ferrule | P12 |  | 6 | Ferrule | 14 | FALSE |  | 🟦⬜️ Blue/White
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

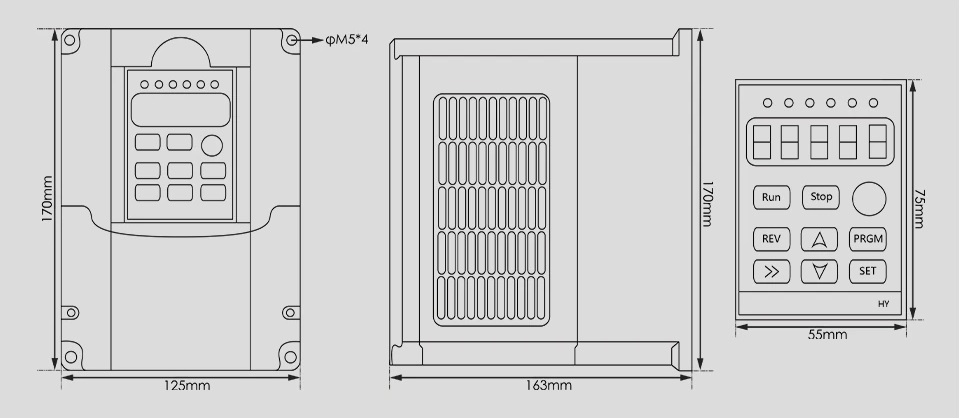
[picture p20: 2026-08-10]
documentation/manuals-datasheets/spindle/HY02D223B-drawing.jpg

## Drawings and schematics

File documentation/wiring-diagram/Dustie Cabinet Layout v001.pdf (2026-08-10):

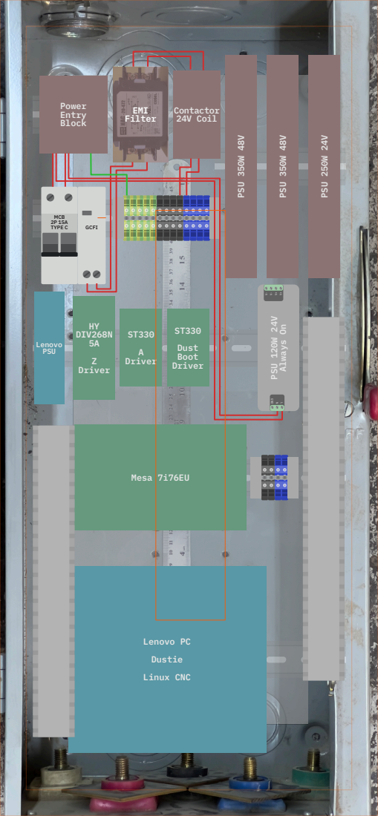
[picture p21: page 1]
EMI Filter; Power Entry Block; Contactor 24V Coil; Lenovo PC; Dustie; Linux CNC; Mesa 7i76EU; HY DIV268N 5A; Z Driver; A Driver; Dust Boot Driver; Lenovo PSU; PSU 350W 48V; PSU 250W 24V; MCB 2P 15A; TYPE C; GCFI; GND; PSU 120W 24V Always On

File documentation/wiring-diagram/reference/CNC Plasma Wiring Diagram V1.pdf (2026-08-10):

01/12/2023

# MESA 7i96S CNC Plasma Wiring Diagram

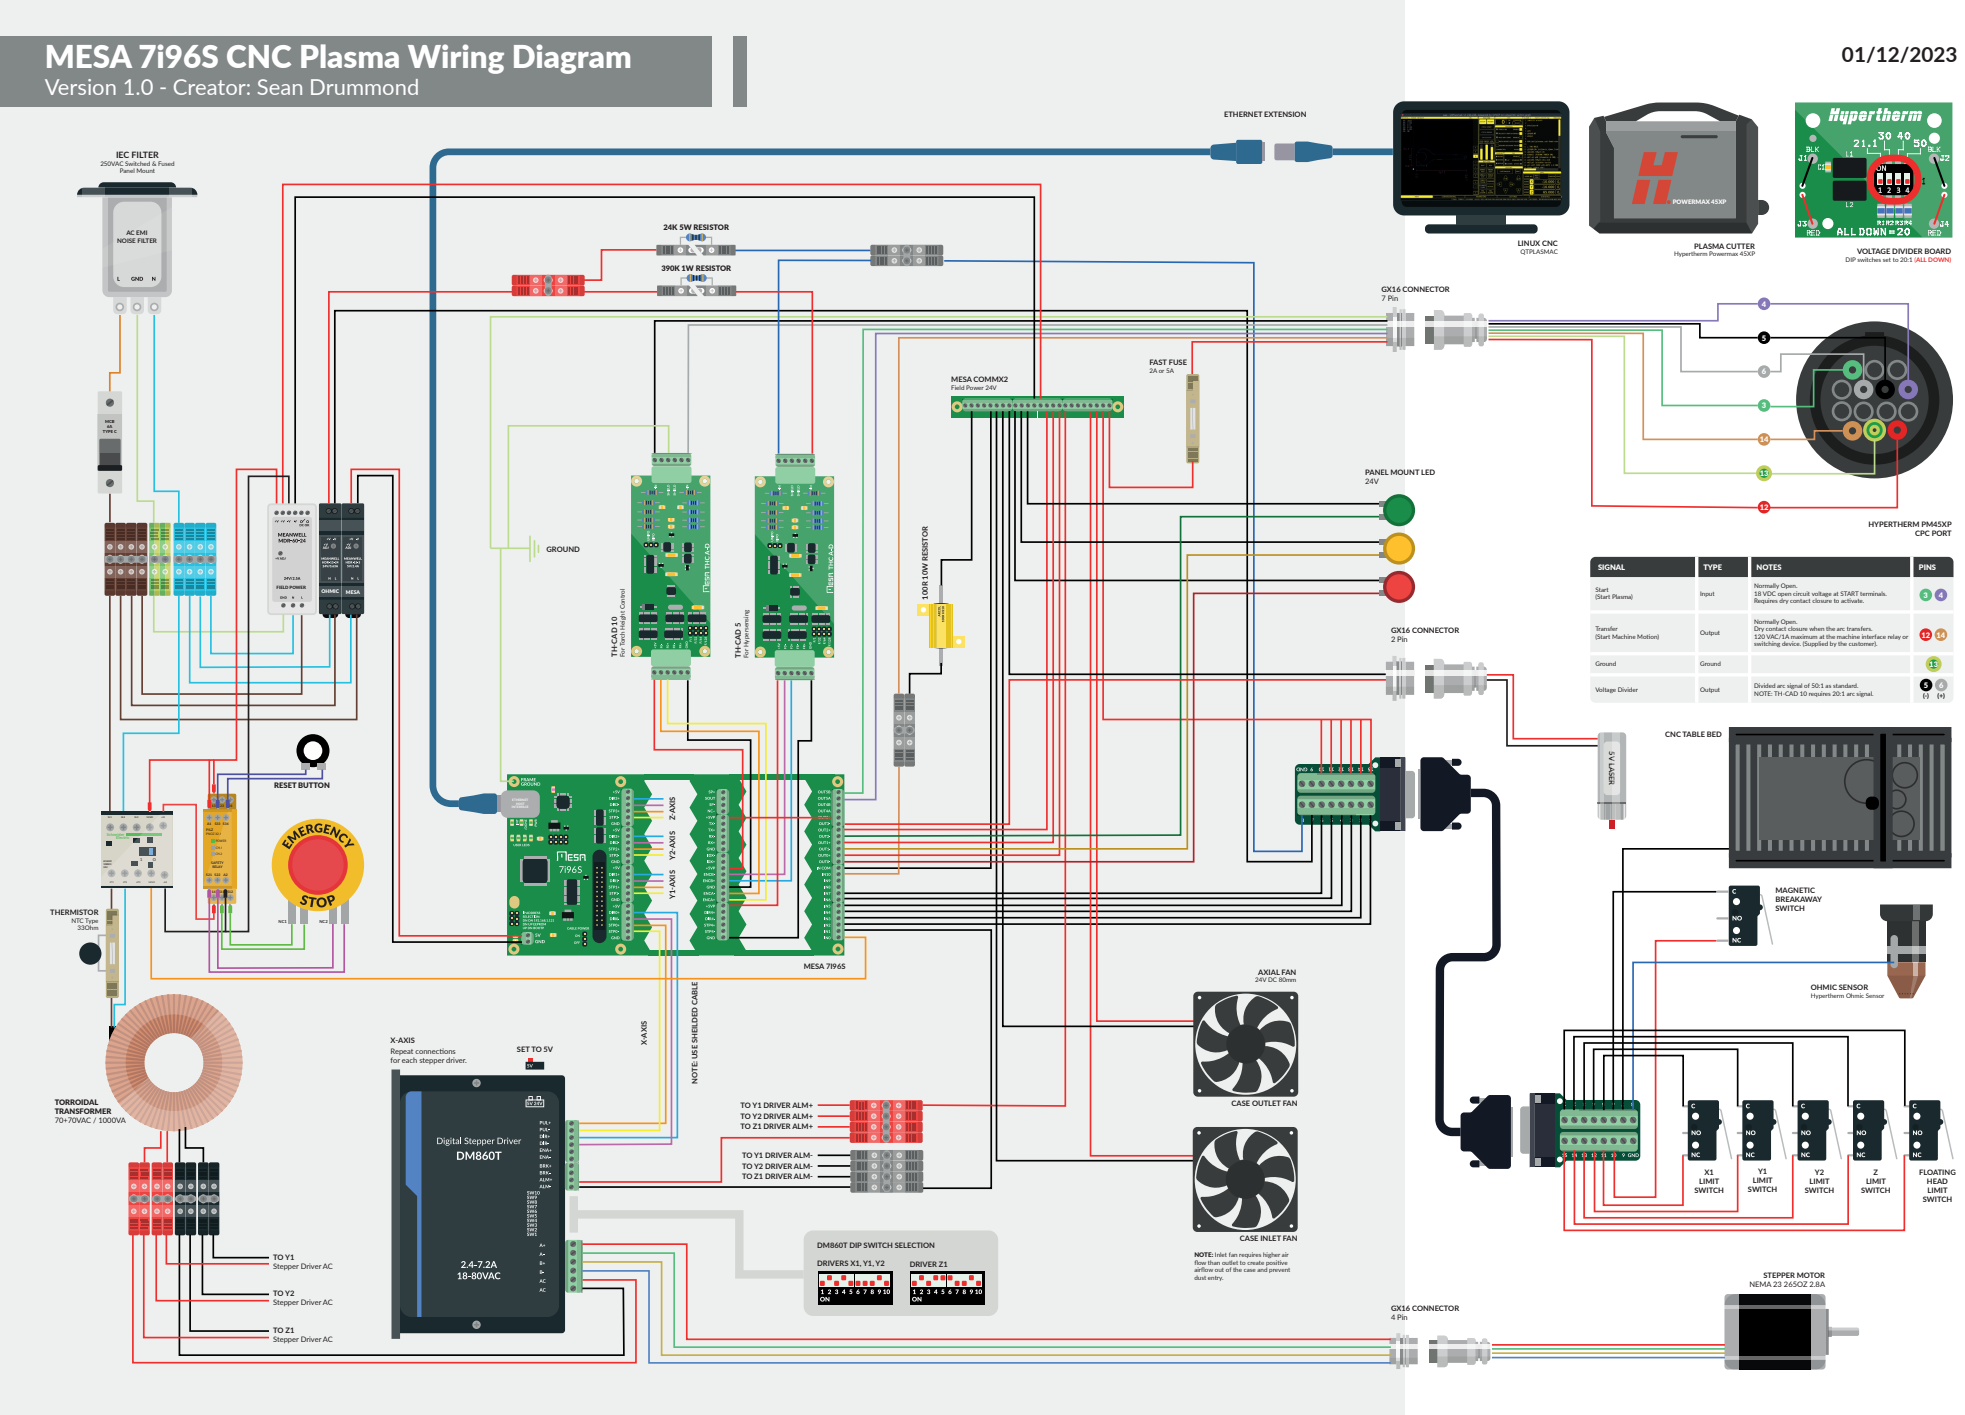
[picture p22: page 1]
AC EMI NOISE FILTER; ETHERNET HOST INTERFACE; POWERMAX 45XP; PILZ PNOZ X2.1; POWER; SAFETY RELAY; Panel Mount; MESA 7I96S; GX16 CONNECTOR 7 Pin; PLASMA CUTTER Hypertherm Powermax 45XP; TH-CAD 10; TH-CAD 5; For Hypersensing; 390K 1W RESISTOR; X1 LIMIT SWITCH; Z LIMIT SWITCH; FLOATING HEAD LIMIT SWITCH; TORROIDAL TRANSFORMER 70+70VAC / 1000VA; MESA COMMX2 Field Power 24V; 24K 5W RESISTOR; SET TO 5V; DRIVERS X1, Y1, Y2; DRIVER Z1; X-AXIS; FAST FUSE 2A or 5A; STEPPER MOTOR NEMA 23 265OZ 2.8A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

Version 1.0 - Creator: Sean Drummond

IEC FILTER 250VAC Switched & Fused

VOLTAGE DIVIDER BOARD
DIP switches set to 20:1 (ALL DOWN)

PANEL MOUNT LED

OHMIC MESA FIELD POWER

Normally Open.
18 VDC open circuit voltage at START terminals.
Requires dry contact closure to activate.

For Torch Height Control

Transfer
(Start Machine Motion)

Dry contact closure when the arc transfers.
120 VAC/1A maximum at the machine interface relay or
switching device. (Supplied by the customer).

Divided arc signal of 50:1 as standard.
NOTE: TH-CAD 10 requires 20:1 arc signal.

CNC TABLE BED

Z-AXIS Y2-AXIS Y1-AXIS

THERMISTOR NTC Type

NOTE: USE SHEILDED CABLE

OHMIC SENSOR
Hypertherm Ohmic Sensor

X-AXIS
Repeat connections
for each stepper driver.

TO Y1 DRIVER ALM+
TO Y2 DRIVER ALM+
TO Z1 DRIVER ALM+

CASE OUTLET FAN

TO Y1 DRIVER ALM-
TO Y2 DRIVER ALM-
TO Z1 DRIVER ALM-

DM860T DIP SWITCH SELECTION

CASE INLET FAN

Stepper Driver AC

NOTE: Inlet fan requires higher air
flow than outlet to create positive
airflow out of the case and prevent
dust entry.

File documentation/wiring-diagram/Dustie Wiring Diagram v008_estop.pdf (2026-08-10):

NO | NC

TB5

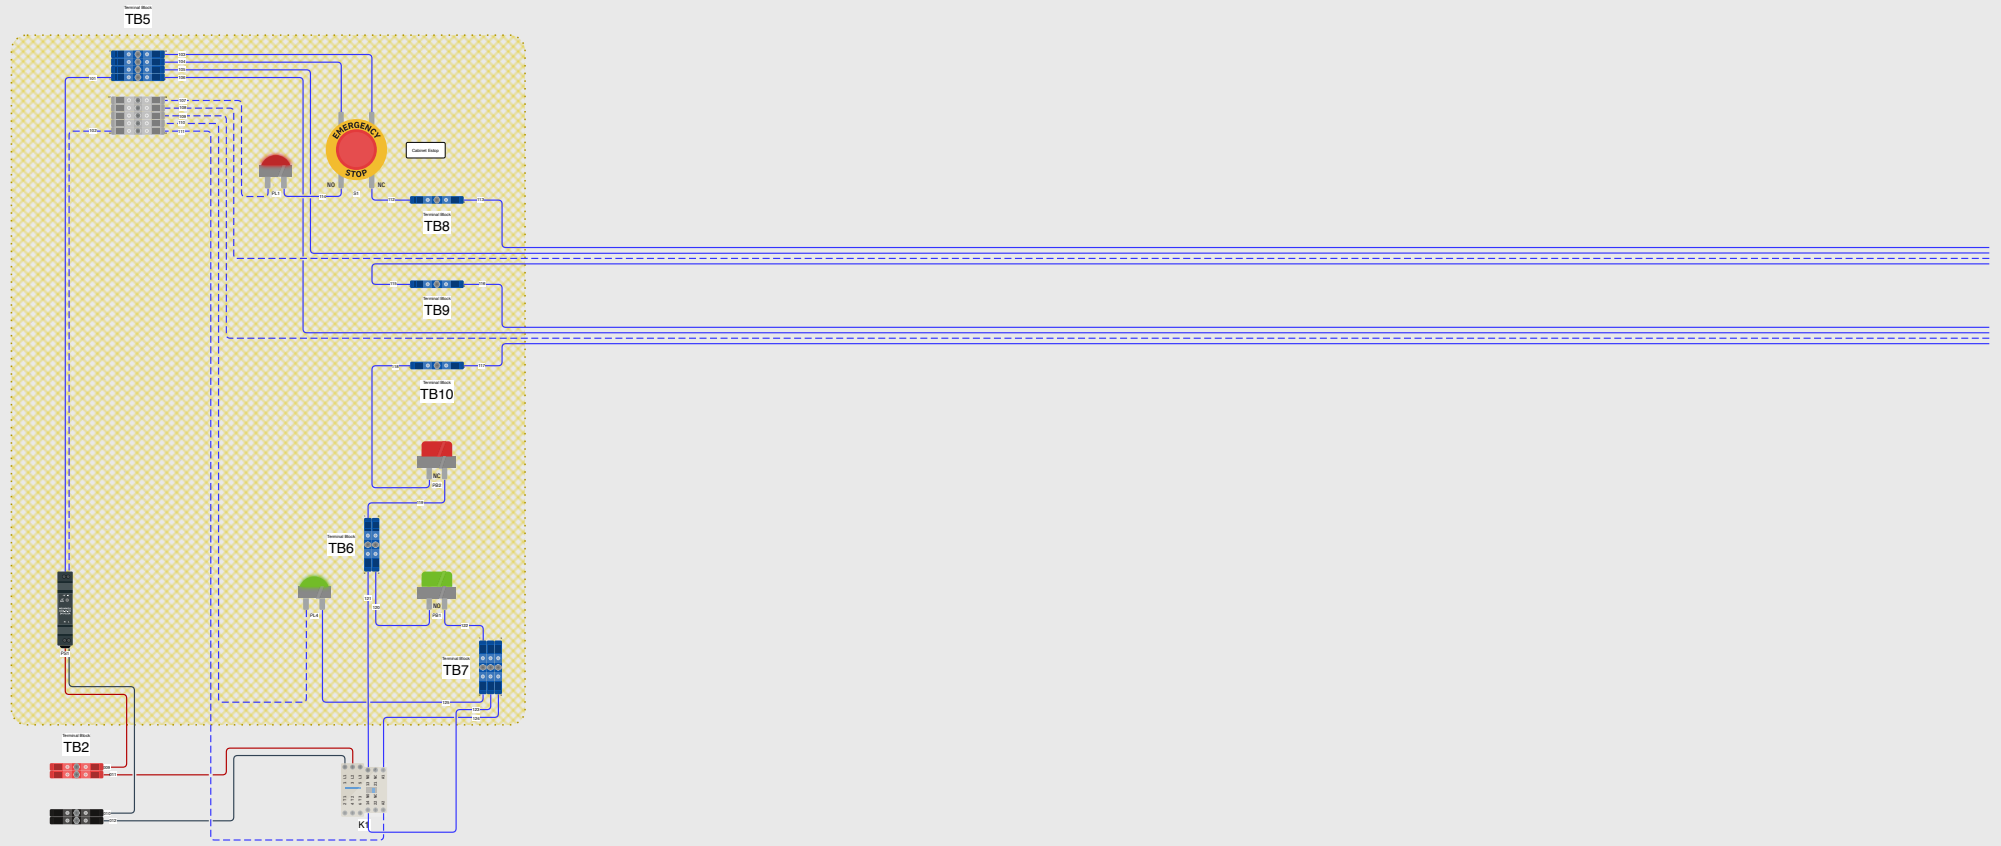
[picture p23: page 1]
STOP; EMERGENCY; Cabinet Estop; Terminal Block TB2; Terminal Block; Terminal Block TB6; Terminal Block TB10; Terminal Block TB8; Terminal Block TB9; Terminal Block TB7

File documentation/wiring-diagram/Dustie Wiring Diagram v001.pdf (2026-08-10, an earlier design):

# Wiring Diagram v001 (WIP)

# Dustie Mk2

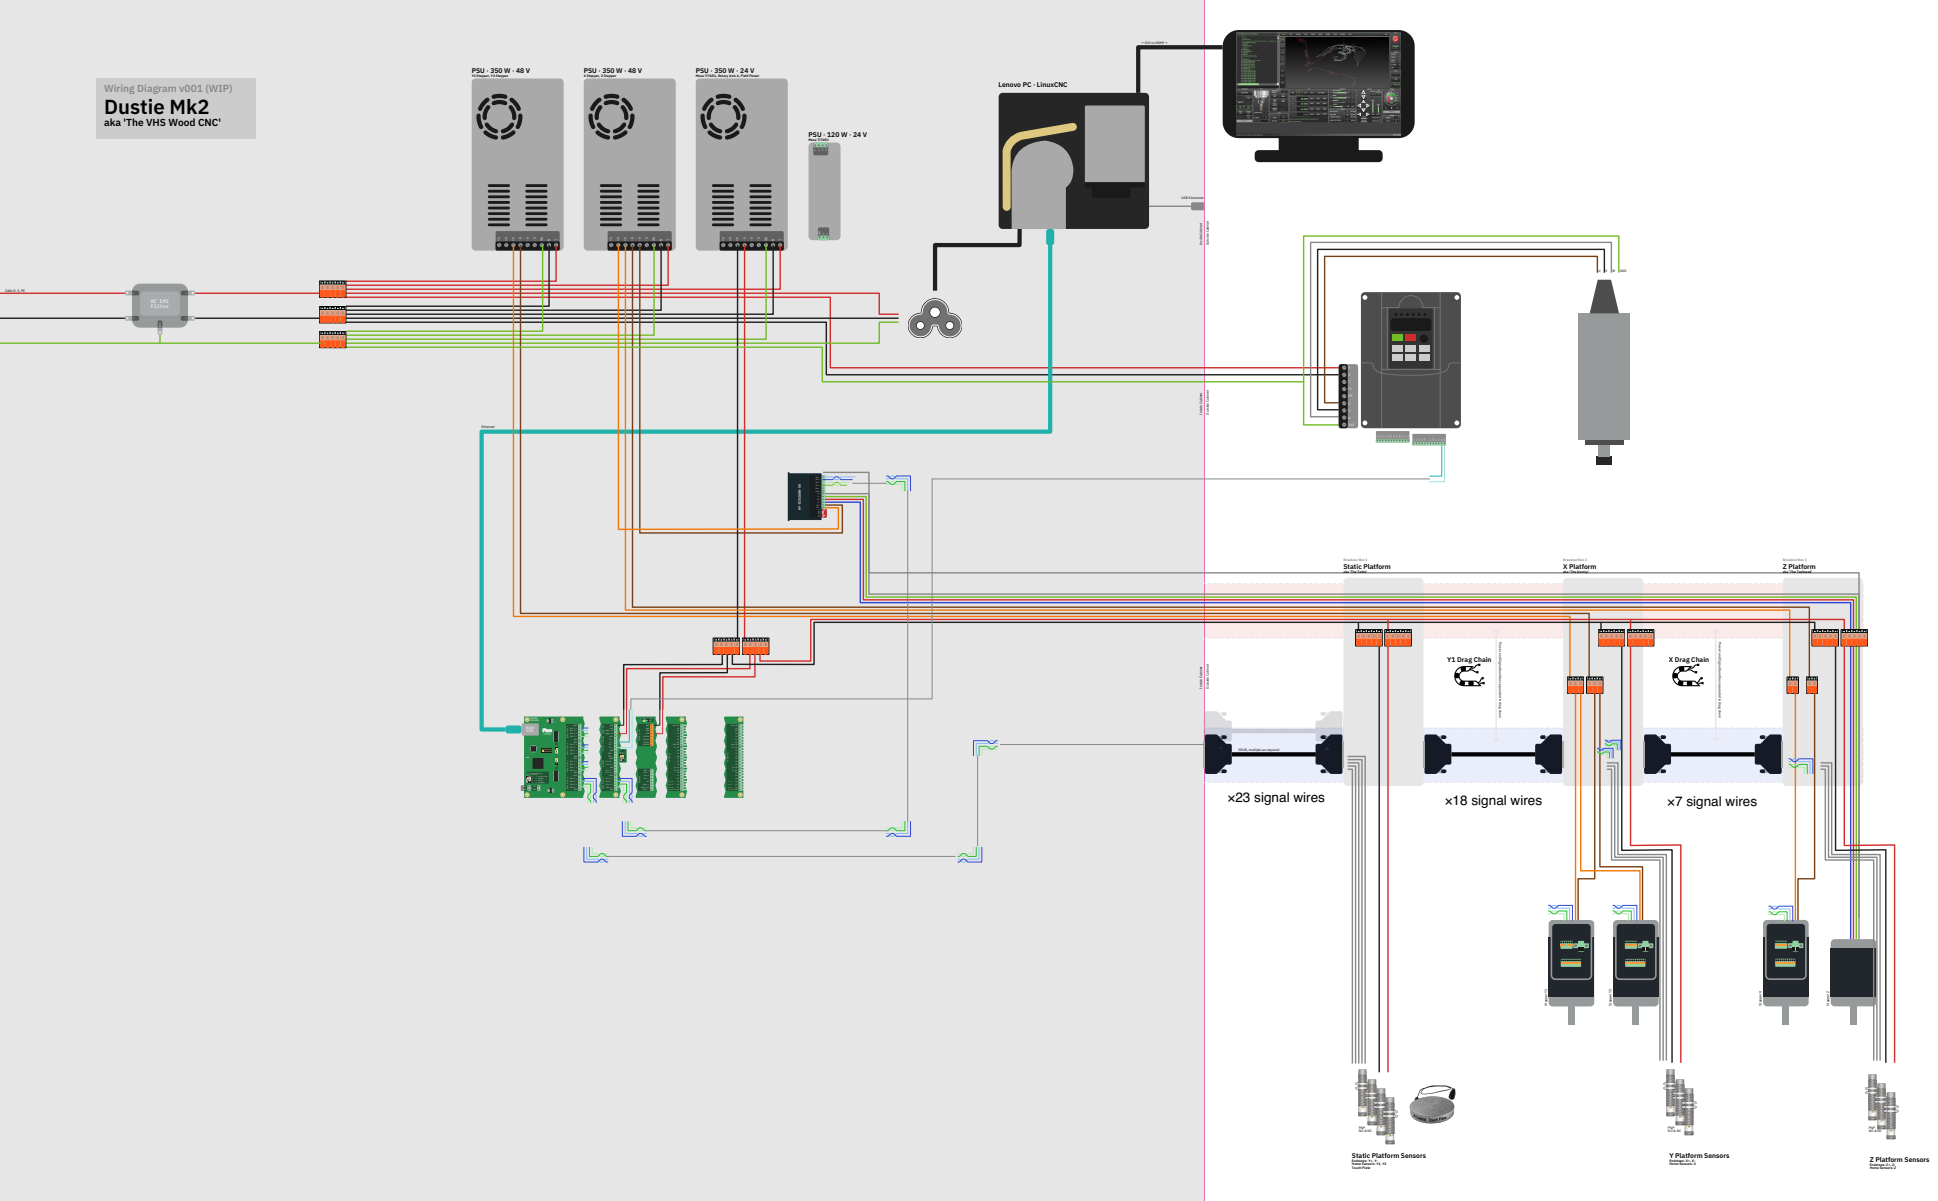
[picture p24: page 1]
GND; AC EMI Filter; PSU · 350 W · 48 V; Y1 Stepper, Y2 Stepper; Inside Cabinet; Outside Cabinet; USB Extension; PNP NO & NC; Y1 Drag Chain; X Drag Chain; Ethernet; X Stepper, Z Stepper; PSU · 350 W · 24 V; PSU · 120 W · 24 V; Mesa 7i76EU; Endstops: Y+, Y- Home Sensors: Y1, Y2 Touch Plate; Breakout Box 1 Static Platform; Breakout Box 2 X Platform; Breakout Box 3 Z Platform; Y Platform Sensors; Endstops: X+, X- Home Sensors: X; Z Platform Sensors; Endstops: Z+, Z- Home Sensors: Z; FRAME GROUND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

← DVI to HDMI →

Mesa 7i76EU, Rotary Axis A, Field Power

Lenovo PC · LinuxCNC

aka 'The VHS Wood CNC'

aka 'The Table'

aka 'The Gantry'

aka 'The Toolhead'

Power and Signal bundles separated in drag chain

COM PWR SEP

DSUB, multiple as required

IP Address Select

Static Platform Sensors

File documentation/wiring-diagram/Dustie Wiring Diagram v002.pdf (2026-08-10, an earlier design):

# Wiring Diagram v002 (WIP)

# Dustie Mk2

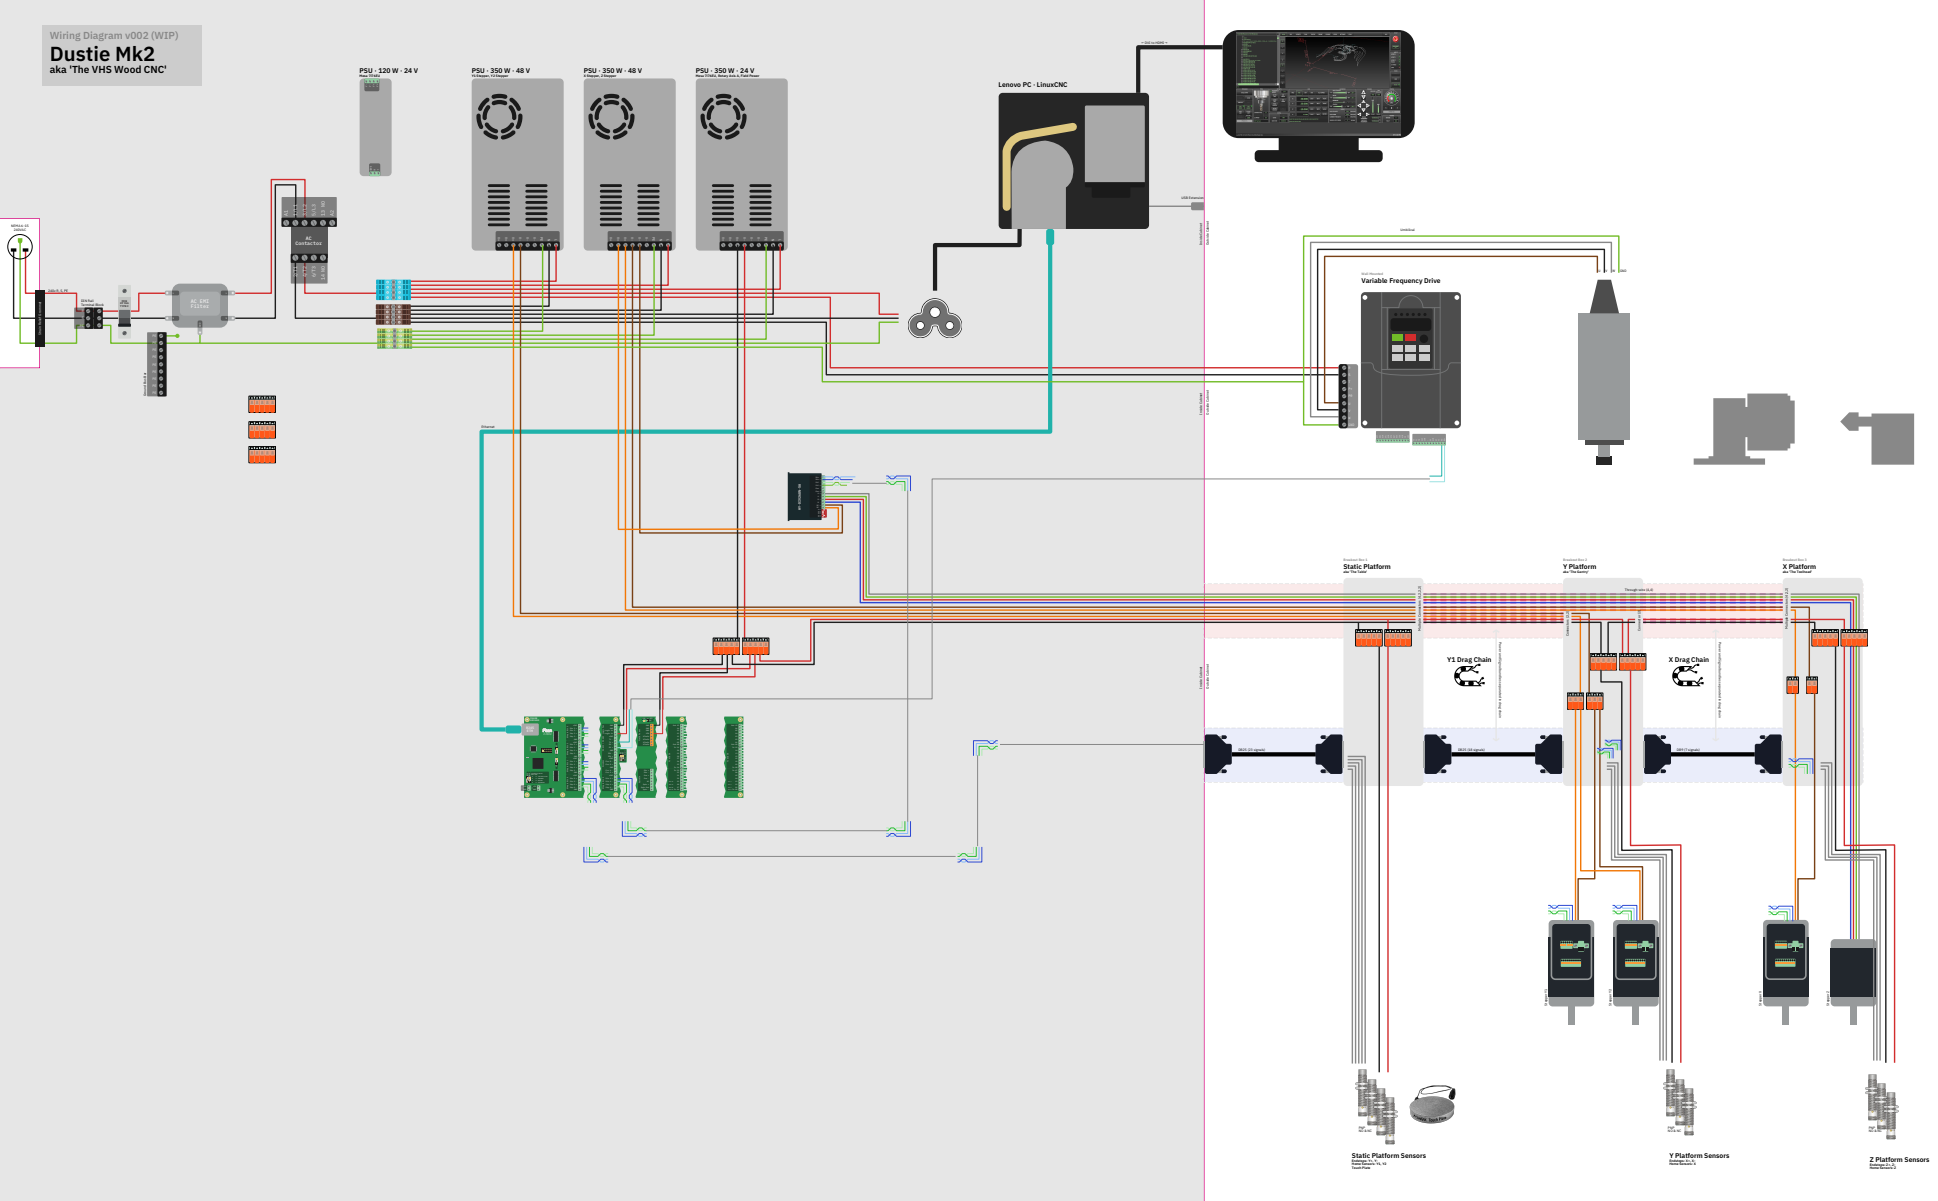
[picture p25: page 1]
GND; AC EMI Filter; PSU · 350 W · 48 V; Y1 Stepper, Y2 Stepper; Inside Cabinet; Outside Cabinet; USB Extension; DB25 (23 signals); DB25 (18 signals); Umbilical; DB9 (7 signals); PNP NO & NC; Y1 Drag Chain; X Drag Chain; Ethernet; X Stepper, Z Stepper; PSU · 350 W · 24 V; PSU · 120 W · 24 V; Mesa 7i76EU; DIN Rail Terminal Block; NEMA 6-15 240VAC; Endstops: Y+, Y- Home Sensors: Y1, Y2 Touch Plate; Breakout Box 1 Static Platform; Multiple Connectors (4,2,2,2); Multiple Connectors (4,2,2)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

← DVI to HDMI →

aka 'The VHS Wood CNC'

Mesa 7i76EU, Rotary Axis A, Field Power

Lenovo PC · LinuxCNC

Wall Mounted
Variable Frequency Drive

Strain Relief Grommet

Ground Bus Bar

aka 'The Table'

aka 'The Gantry'

aka 'The Toolhead'

Power and Signal bundles separated in drag chain

COM PWR SEP

IP Address Select

Static Platform Sensors

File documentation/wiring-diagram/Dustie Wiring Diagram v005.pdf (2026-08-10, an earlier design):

NO | NC

NC

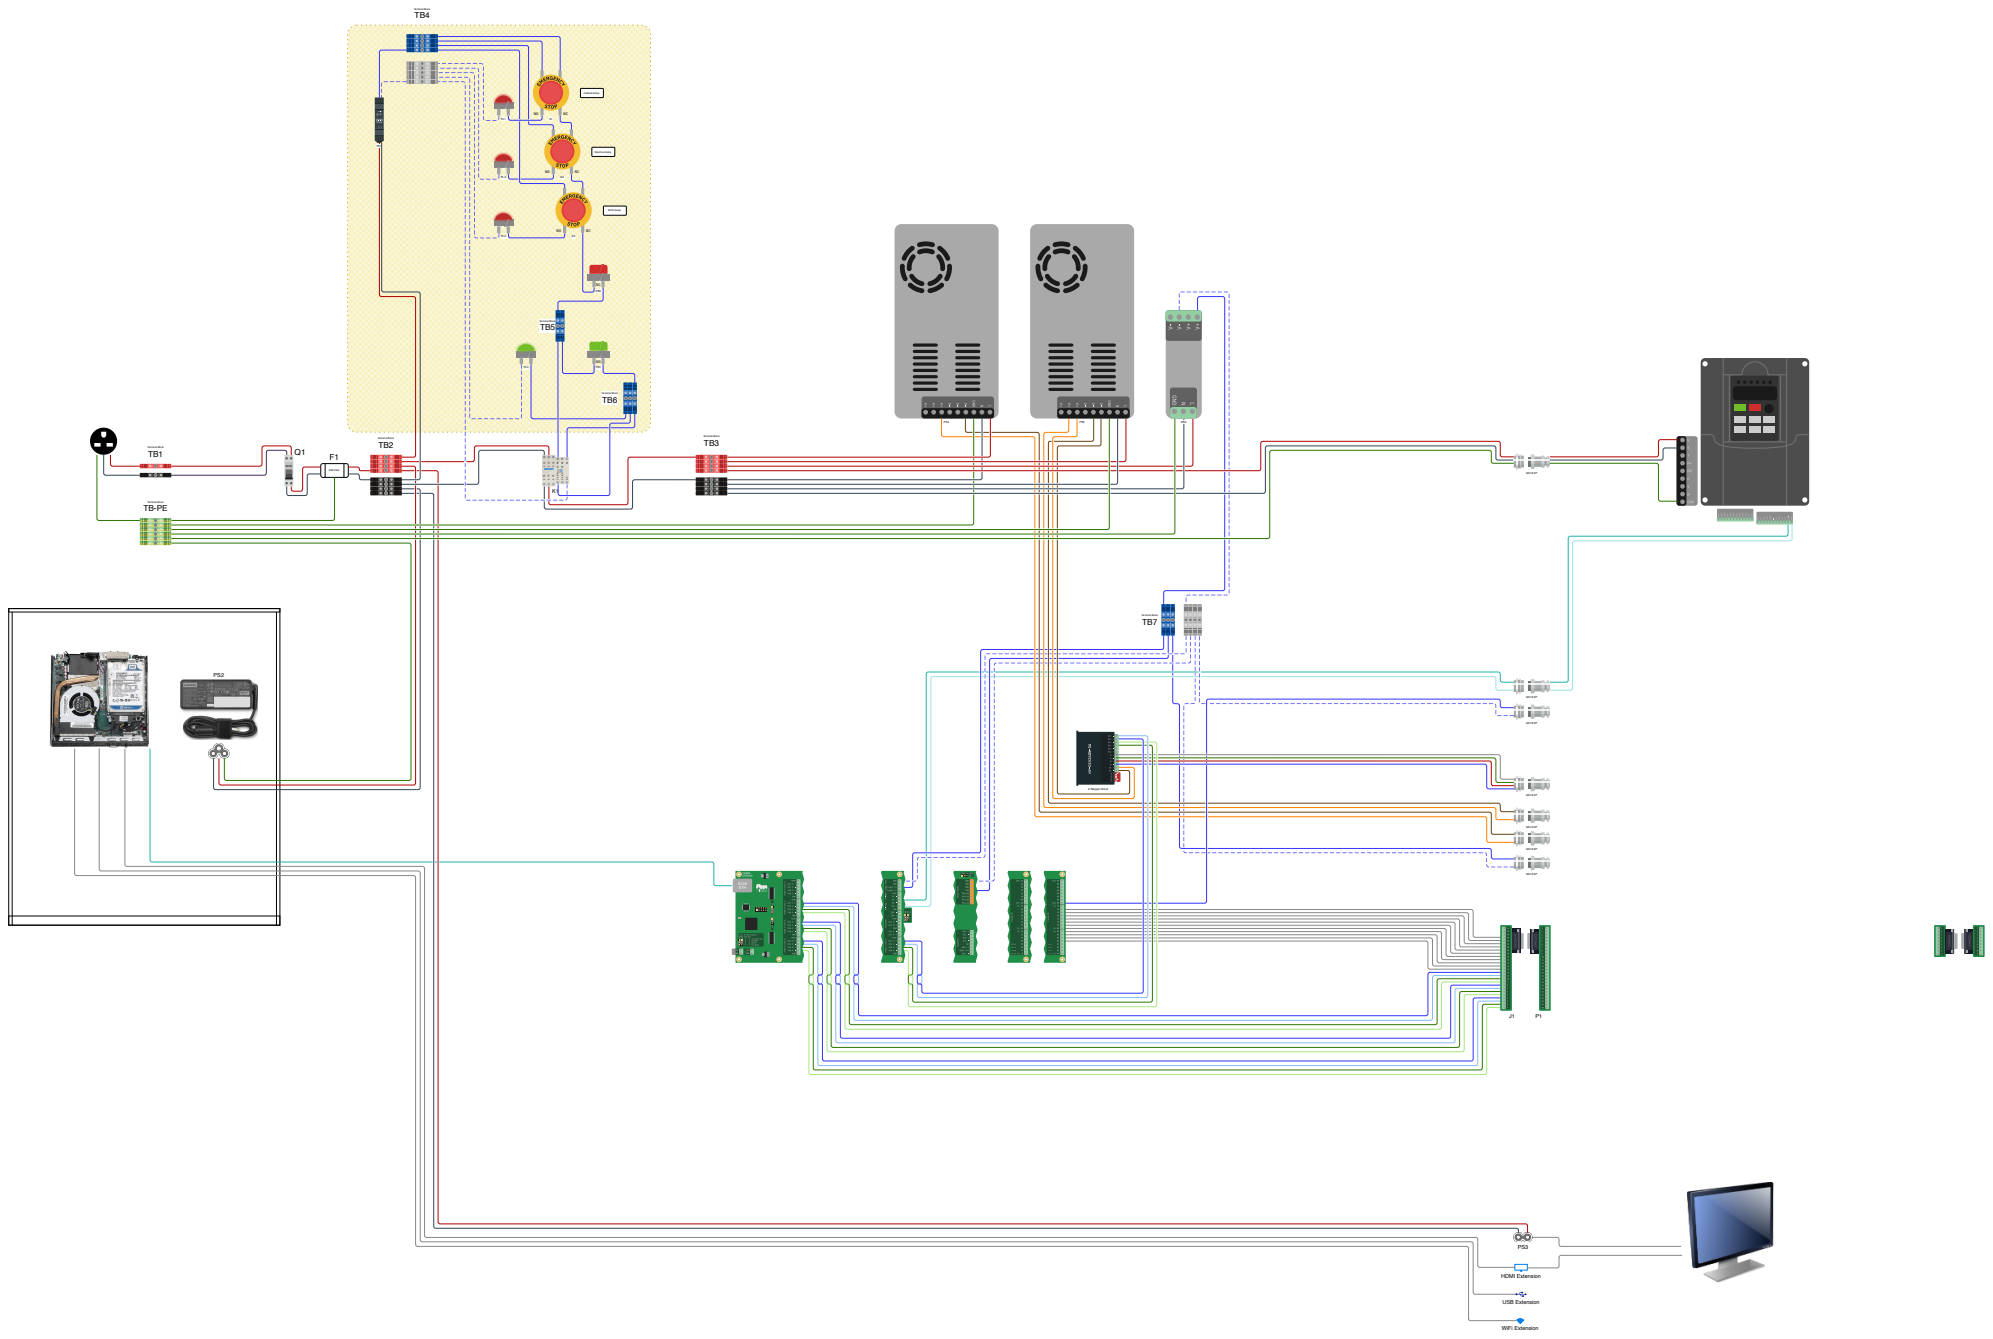
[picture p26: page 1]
Terminal Block TB5; Terminal Block TB6; MCB; STOP; EMERGENCY; Cabinet Estop; Machine Estop; MPG Estop; EMI Filter; Terminal Block TB1; Terminal Block TB2; Terminal Block TB3; Terminal Block TB4; Terminal Block TB7; Z Stepper Driver; HDMI Extension; USB Extension; WiFi Extension

Terminal Block TB-PE
